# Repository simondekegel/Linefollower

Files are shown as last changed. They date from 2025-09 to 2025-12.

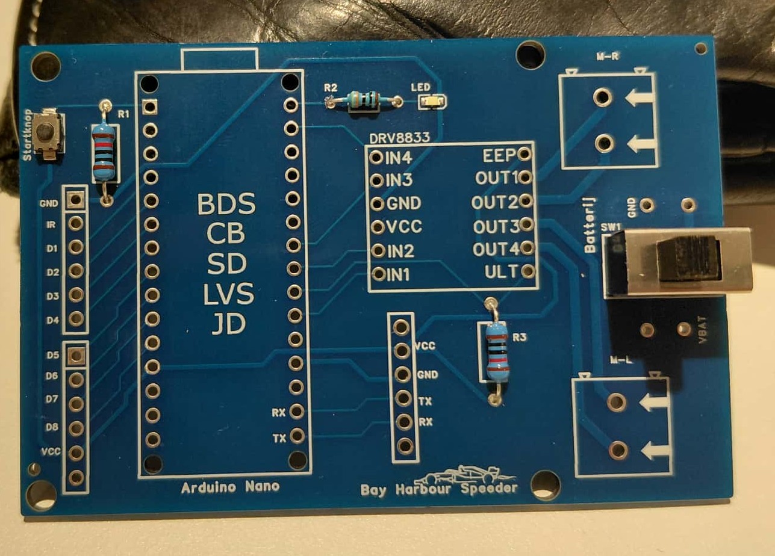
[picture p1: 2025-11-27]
images/519357136-53358113-0e21-4ff5-8163-3b82a2c3a71a.jpeg

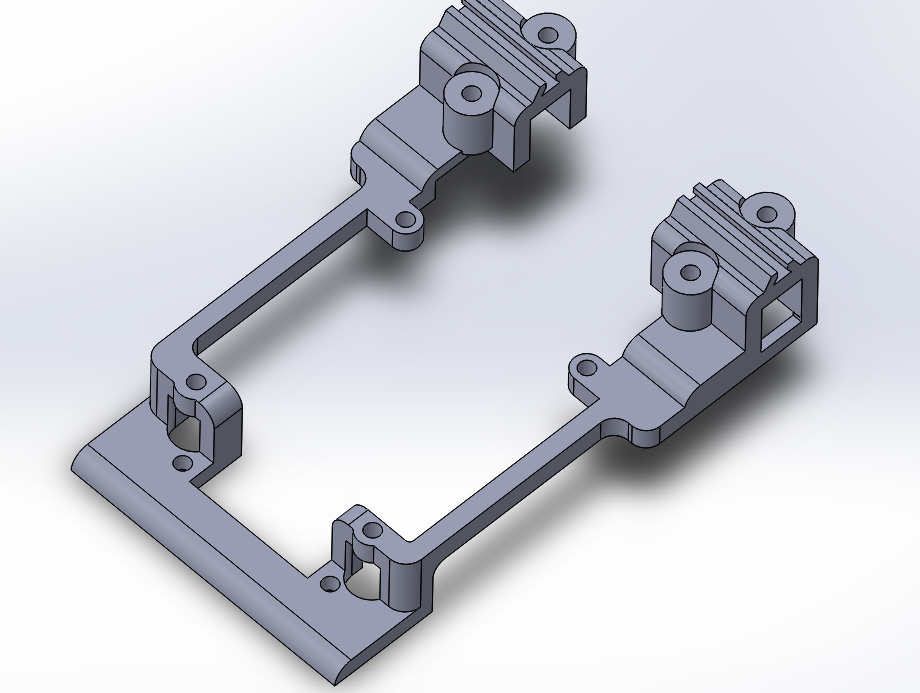
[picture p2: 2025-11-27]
technische tekeningen/mechanisch/517844766-8e0d4717-322a-4456-812b-64dfd0e3311b.png

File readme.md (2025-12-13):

# LineFollower

516304872-0ebdff40-2b66-4d8c-be46-cdccf1087acf

## specifications

microcontroller: Arduino nano (clone)

motors: N20---30:1---500RPM 

h-bridge: DRV8833

sensors: HY-S301

batteries: 2x 18650 lipo

wireless communication: HC-08 

distance sensor - motors: 9.92cm

weight: 214gr

speed: 0.72m/s

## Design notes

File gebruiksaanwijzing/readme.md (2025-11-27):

# Gebruiksaanwijzing

### opladen / vervangen batterijen
Batterijen worden opgeladen met een lader die specifiek ontworpen is voor 18650 (Lithium) batterijen.
Voor de batterijen kunnen worden ingestoken of verwijderd moet er gecontroleerd worden of de hoofdschekelaar van de pcb uitstaat (naar buitenste stand van de schakelaar)

### draadloze communicatie
#### verbinding maken
We gebruiken een Hc-08, deze kan een signaal spanning aan van 3,2-6V op zijn TX & RX pinnen. En 3,2-6V op zijn VCC. 

Een Hc-08 werkt op BLE (Bluetooth low energy), deze is dus compatible voor zowel android als iphone apparaten.

De applicatie die gebruikt werdt om de commandos te sturen is "serial bluetooth terminal", is beschikbaar op de google playstore en zou ook op de iphone app store beschikbaar moeten zijn.

#### commando's
debug : debug

start : run on

stop  : zolang je een niet bekend commande typed zal hij stoppen

set cycle [µs]  : set cycle ...

set power [0..255]  : set power ...

set diff [0..1]  : set diff ...

set kp [0..]  set kp ...

set ki [0..]  set ki ...

set kd [0..]  set kd ...

calibrate black  : calibrate black

calibrate white  : calibrate white

### kalibratie
uitleg kalibratie  

### settings
De robot rijdt stabiel met volgende parameters: 

| KP: 30  | KI: 0.1 | KD: 0.35 | diff:  0.6 | Power: 130 | snelheid: 0.63m/S |

### start/stop button
De start knop is aanwezig op de pcb, deze is geplaatst naast de sensoren (rechts voor). Deze knop zal de zelfde variable sturen als het commando run on. Om de follower te doen stoppen kan je een commande sturen of hem boven een wit blad houden (dit is zodat hij stopt met rijden als hij geen zwarte lijn meer ziet).

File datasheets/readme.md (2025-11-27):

datasheets of the components used in this project

Datasheet van de DRV8833 [drv8833-datasheet.pdf](https://github.com/user-attachments/files/23694670/drv8833-datasheet.pdf)

Datascheet van de Arduino nano [A000005-datasheet.pdf](https://github.com/user-attachments/files/23694715/A000005-datasheet.pdf)

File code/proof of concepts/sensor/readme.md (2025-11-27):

# Sensoren proof of concept
minimale hard- en software die aantoont dat minimaal 6 sensoren onafhankelijk van elkaar kunnen uitgelezen worden (geen calibratie, normalisatie of interpolatie). Hierbij moet een zo groot mogelijk bereik van de AD converter benut worden (indien van toepassing)

Benodigdheden

HY-S301
Arduino Nano R3
Stappenplan

Sluit de sensor aan de arduino volgens het aansluitschema aan.
Verbind de arduino met de pc en upload het programma in de arduino.
test met een wit oppervlak of de waarden veranderen van de sensoren.

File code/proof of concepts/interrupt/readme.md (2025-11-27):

# start/stop interrupt proof of concept
Dit is een simpele minimale code die aantoont hoe da een toggle functie kan geprogrammeerd worden met een knop en led. 
Uitgangen zijn gekozen a.d.h.v. het elektronisch schema.

De knop wordt uitgelezen en zal een bool (run) op initieel op 1 zetten bij het 1ste gebruik.
Bij de 2de druk, als run = 1, zal diezelfde knop run op 0 zetten waardoor de led ook zal doven.

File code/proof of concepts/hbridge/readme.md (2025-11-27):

# H-Bridge proof of concept

Welkom in de readme van het H-brug gedeelte van de linefollower.

De H-brug gebruikt een DRV8833 microchip. Deze heeft op het breakoutbord 4 ingangen, 4 uitgangen, VCC, GND, EEP & ULT.

De ingangen en uitgangen spreeken opzich, zeer belangrijk bij de ingangen is dat de pwm's op de zelfde clock snelheid zitten. PWM 3, 5, 6 & 11 hebben een 8bit clocksnelheid. PWM 9 & 10 hebben een 16bit clocksnelheid. ALs 2 soorten clocksnelheden worden gebruikt zullen de motoren een verschillende snelheid hebben.

De EEP pin wordt aan de VCC (5V) van de arduino gekoppeld, dit moet zeker verbonden worden anders zal de H-brug niet werken. Als de EEP geen voeding krijgt zal de H-brug in sleep modus staan waardoor de OUT's niet zullen schakelen.

De Ult pin wordt met een pull-up weerstand geschakeld, deze dient als fout detectie. Als de H-brug normaal werkt zal deze een hoog signaal hebben waardoor de arduino een laag signaal leest. Als er een interne fout in de H-brug is zal de uitgang laag zijn waardoor de arduino een hoog signaal zal lezen. Dit zullen we a.d.h.v. een HC-05 door sturen naar een gsm.

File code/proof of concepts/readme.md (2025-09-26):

# Proof of Concepts

Een proof of concept is een combinatie van minimale hard- en software om eenvoudig aan te tonen dat iets werkt.  
Proof of concepts kunnen enerzijds als eerste poging dienen om een bepaald onderdeel van het project werkend te krijgen. Anderzijds kunnen ze tijdens het debuggen van het finale project dienen als test om eventuele hardware problemen te elimineren bij onduidelijke problemen.
<br />  
<br />
Een proof of concept bestaat uit
* een elektronisch schema (indien van toepassing)
* minimale code om de voorop gestelde zaken te demonstreren
* minimale uitleg / aandachtspunten
<br />
De elektronische schakelingen van de proof of concepts komen bij voorkeur overeen met deze van de uiteindelijke linefollower, zodat de code zonder aanpassingen op het finale project kan draaien.

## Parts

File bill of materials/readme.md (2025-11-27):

## bill of materials
<br />

|volgnummer|naam|omschrijving|nieuw/recup|kostprijs/stuk|aantal|subtotaal|
|---|----|---|---|---|---|---|
| 1| HC-08 Bluetooth module met adapter - clone| bluetooth module | nieuw | €8.5 |  1 |  €8.5 |
| 2| Arduino Nano R3 - kloon - met headers| Arduino Nano | nieuw |  €8.60 |  1 |  €8.60 |
| 3| Female header stackable 6 pin (5x nodig) |10x Female headers 6 pin | nieuw |  €2.85 | 0.5 | €1.425 |
| 4| DRV8833|dubbele H-brug | nieuw | €3 | 1 |€3 |
| 5| HY-S301 | 8x IR Lijn Tracking Module | nieuw | €3.50 | 1 | €3.50 |
| 6| Aslong JGA12-N20-30 DC-Transmissiemotor 6V - 500RPM| motor 30:1 | nieuw |  €4.50 | 2 |  €9.00 |
| 7| 15 Pins header Female | fermale headers 15 pinss | nieuw |  €0.31 | 2 | €0.62 |
| 8| 18650 | batterij | nieuw | €1.45 | 2 | €2.90 |
| 9| 2x 18650 Batterijhouder met klemkontacten en losse draden | Batterijhouder |  nieuw | €1.59 | 1 |  €1.59 |
| 11| | klemschroefblok 2 pins | recup | €0.55 |  2 |  €1.10 |
| 12| JLCPCB| zelf ontworpen pcb | nieuw | €4.245 |  1 | €4.245 |
| 13|  wielen  | aliexpress wielen | nieuw | €0.98 |  2 | €1.96 |
| | | | | | | |
| Tootaal| |  (zonder verzend kosten!!!!!) | | | | €46,44 |

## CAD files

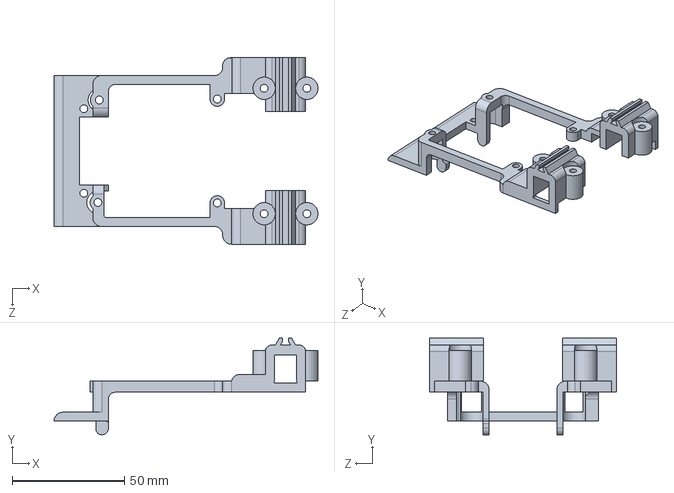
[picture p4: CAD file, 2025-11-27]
technische tekeningen/mechanisch/Frame V9.SLDPRT
117.5 x 43.0 x 83.0 mm

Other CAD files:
technische tekeningen/mechanisch/Frame V9.STL

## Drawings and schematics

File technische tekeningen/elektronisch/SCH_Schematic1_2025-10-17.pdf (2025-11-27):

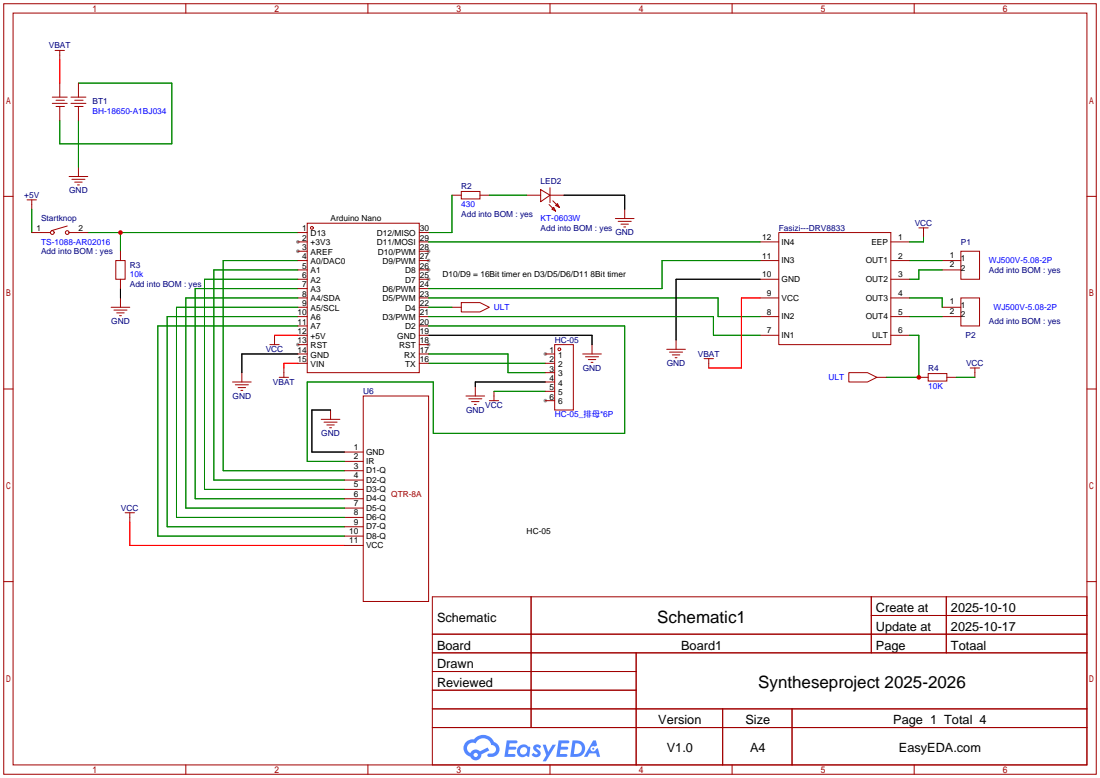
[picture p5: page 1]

Startknop
Add into BOM : yes

Schematic | Schematic1 | Create at | 2025-10-10

Update at | 2025-10-17

Board | Board1 | Page | Totaal
Drawn | | Syntheseproject 2025-2026
Reviewed

Version | Size | Page 1 Total 4
V1.0 | A4 | EasyEDA.com

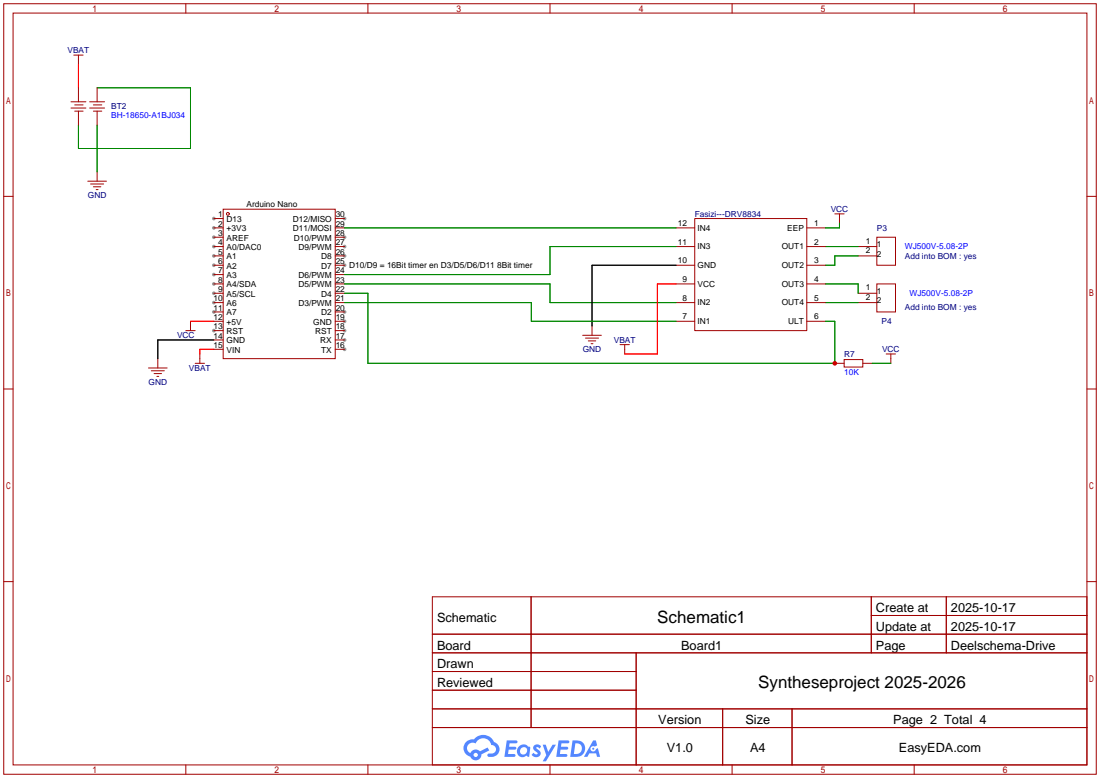
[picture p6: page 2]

Schematic | Schematic1 | Create at | 2025-10-17

Update at | 2025-10-17

Board | Board1 | Page | Deelschema-Drive
Drawn | | Syntheseproject 2025-2026
Reviewed

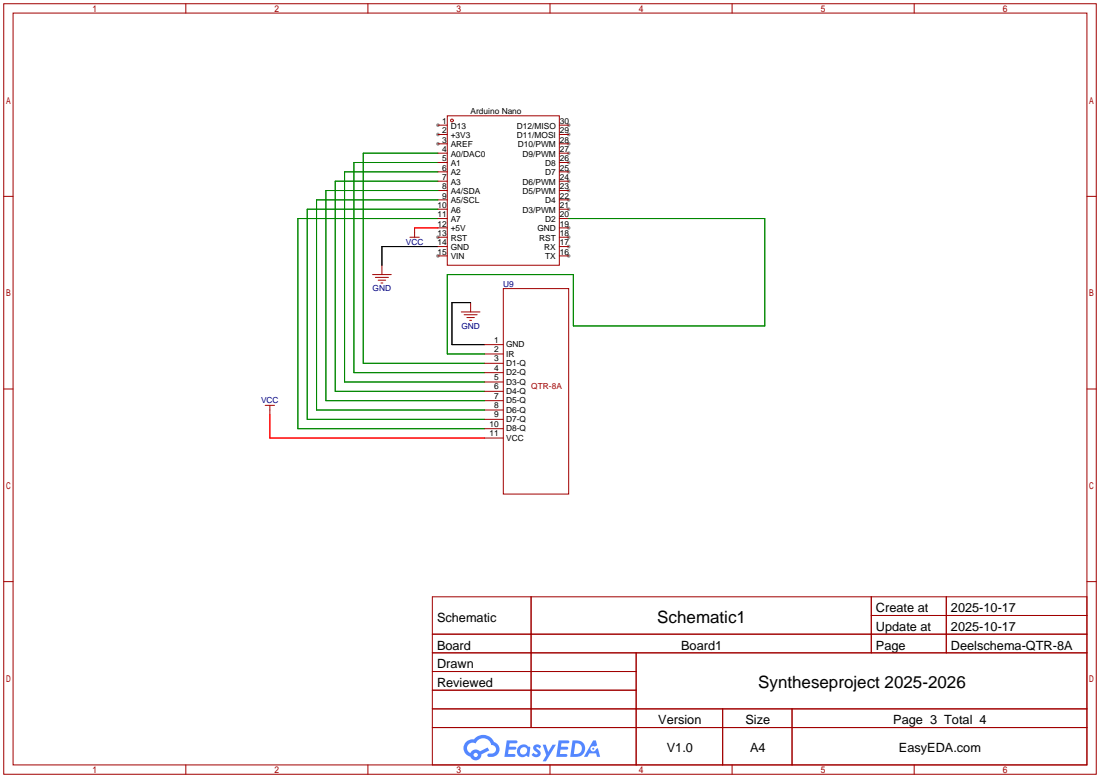
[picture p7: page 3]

Schematic | Schematic1 | Create at | 2025-10-17

Update at | 2025-10-17

Board | Board1 | Page | Deelschema-QTR-8A
Drawn | | Syntheseproject 2025-2026
Reviewed

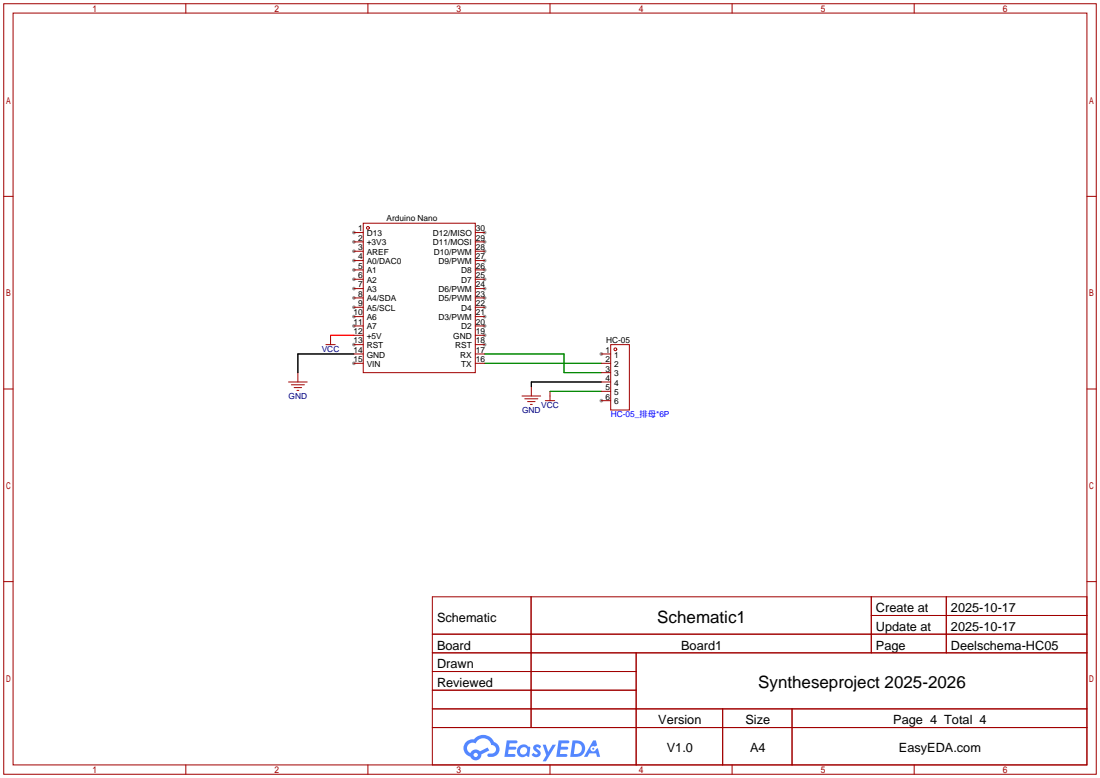
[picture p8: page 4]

Schematic | Schematic1 | Create at | 2025-10-17

Update at | 2025-10-17

Board | Board1 | Page | Deelschema-HC05
Drawn | | Syntheseproject 2025-2026
Reviewed

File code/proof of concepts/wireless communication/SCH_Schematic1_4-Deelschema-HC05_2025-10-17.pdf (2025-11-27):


Schematic | Schematic1 | Create at | 2025-10-17

Update at | 2025-10-17

Board | Board1 | Page | Deelschema-HC05
Drawn | | Syntheseproject 2025-2026
Reviewed

Version | Size | Page 4 Total 4
V1.0 | A4 | EasyEDA.com

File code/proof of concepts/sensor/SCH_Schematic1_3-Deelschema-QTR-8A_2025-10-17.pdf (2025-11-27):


Schematic | Schematic1 | Create at | 2025-10-17

Update at | 2025-10-17

Board | Board1 | Page | Deelschema-QTR-8A
Drawn | | Syntheseproject 2025-2026
Reviewed

Version | Size | Page 3 Total 4
V1.0 | A4 | EasyEDA.com

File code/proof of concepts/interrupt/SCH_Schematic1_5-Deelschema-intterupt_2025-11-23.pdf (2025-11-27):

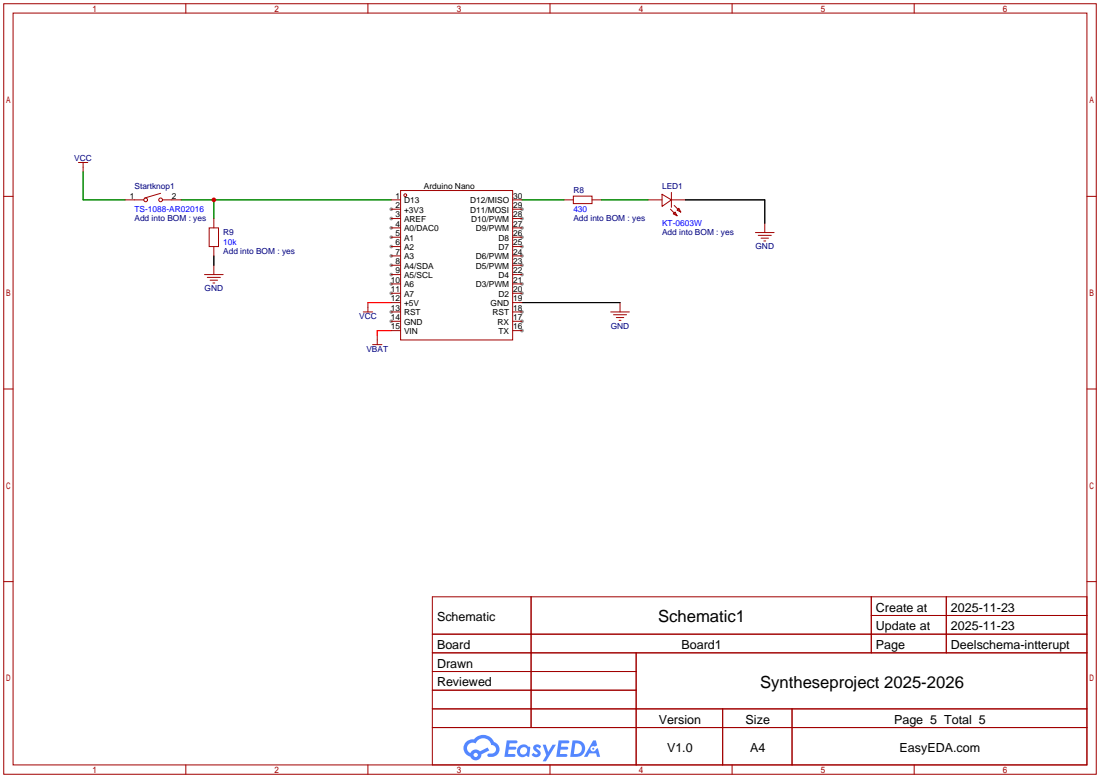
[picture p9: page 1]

Add into BOM : yes

Schematic | Schematic1 | Create at | 2025-11-23

Update at | 2025-11-23

Board | Board1 | Page | Deelschema-intterupt
Drawn | | Syntheseproject 2025-2026
Reviewed

Version | Size | Page 5 Total 5
V1.0 | A4 | EasyEDA.com

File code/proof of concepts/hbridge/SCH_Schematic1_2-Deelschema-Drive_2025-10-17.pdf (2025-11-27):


Schematic | Schematic1 | Create at | 2025-10-17

Update at | 2025-10-17

Board | Board1 | Page | Deelschema-Drive
Drawn | | Syntheseproject 2025-2026
Reviewed

Version | Size | Page 2 Total 4
V1.0 | A4 | EasyEDA.com

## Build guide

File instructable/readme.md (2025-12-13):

# Instructable

Een instructable is een stappenplan - zonder verdere uitleg - hoe je vertrekkend van de bill of materials en gebruik makend van de technische tekeningen de robot kan nabouwen. Ook de nodige stappen om de microcontroller te compileren en te uploaden staan beschreven.  

### stap 0
Bestel de componenten uit de BOM, zoveel mogelijk van dezelfde leverancier (tinytronics).

De pcb, onder technische tekeningen -> elektronisch vindt je de elektronische schemas als de pcb file die je kan importeren in easyeada.

De pcb is ontworpen om de weerstanden, drukknop, schakelaar en led er op telaten zetten tijdens productie en is dus mee gerekend in de pcb kosten.
(dit moet je tijdens het bestellen aanduiden want dit wordt niet automatisch gedaan)

### stap 1
test de componenten uit a.d.h.v. de schemas en codes onder de tab code -> proof of concepts. 
deze zullen een goede werking demonstreren van de componenten.

DRV8833 wordt best eerst getest met led's.
Aangeraden om de sensor op een vaste hoogt te monteren om een duidelijk verschil te zien tussen zwart en wit.

### stap 2
Soldeer de female headerds en terminals op de pcb als de draden op de sensor, aangeraden om 0.8mm² stijvedraden te gebruiken (recup van sgg kabel).

### stap 3
Print het frame dat te vinden is onder technische tekeningen -> mechanisch. 
Hier zal je een stl bestand vinden als een solidworks tekening voor als je zelf aanpassingen wilt uitvoeren.
(spoiler stl is ook beschikbaar)

### stap 4
monteer alle componeten op het frame met M3 bouten en moeren. je moet er maar 5 van elk gebruiken (2 voor de sensor, 2 voor de batterijhouder en 1 voor de pcb).

### stap 5
Als de motoren en batterijhouder op het frame zijn bevestigd kan je de draden hiervan solderen.

LET GOED OP!!!!
Batterijhouder: de rode draden van de batterijhouder zullen wij zien als + en zwart als -. We solderen de rode draden op de pcb links van de schakelaar (aan de kant waar VBAT staat) en de zwarte draden rechts van de schakelaar (aan de kant waar GND staat). 
De batterijen zijn via de pcb in serie geschakeld dus we mogen ze extern NIET KRUISEN, ik heb de buitenste batterij aan de buitenste pads gesoldeerd en de batterij aan de binnen kant aan de binnenste pads.

Motoren: de motoren kunnen simpel gesoldeerd worden als ze geklemmed zitten in het frame. hoe dat deze aangesloten worden is de bovenste draden aan de buitenste terminal slots en de onderste aan de binneste slots van hun respectievelijke terminals (links-links & rechts-rechts).

### stap 6 
Upload de basis code dat te vinden is in code->basis. download alle 4 de bestanden en zet deze in dezelfde map. anders zal het programma niet werken.
dit programma bevat een basis werking van het EEPROM geheugen als normalistatie en interpolatie van de sensor en een P regelaar. 

commandes zijn terug tevinden in de gebruikersaanwijzing.

### stap 7
print de parcours. steek de batterijen in de houder (ROOD +, ZWART -) en zet de schakelaar naar binnen toe. 
als alles goed is verlopen zullen nu signalisatie leds van de arduino nano, hc-08 en motordrive branden.

### stap 8
zet de follower op een wit stuk van het parcour en calibreer wit, doe dit ook voor zwart.

Zet intitieel  power= 80, kp= 10 en diff op 0,4.
Nu ben je klaar om te rijden. 
Stuur het commande "run on" and watch the magic happen.

Je zal de instellingen langzaam moeten tweaken want de waarde zullen voor iedereen verschillen.

### stap 9
upload de final code, deze heeft ook een I & D regelaar.
De follower heeft nu de mogelijkheid om de lijn vlotter tevolgen.

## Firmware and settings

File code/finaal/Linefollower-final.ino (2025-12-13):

/*
 ----------INSTRUCTIES HOE JE DEZE CODE GEBRUIKT EN WAARDES AANPAST------------
 -----------------------------------CB-----------------------------------------
 voor de waardes intestellen (diff, power, cycle,...) stuur je in de serial monitor => "set (naam) (value)"
 voor het instellen van de cyletime stuur in de serial monitor "set cyle 1000000", cycle time voor goede werking <500
 *
 voor calibratie sensor wit stuur in serial monitor "calibrate white" ----aangeraden om voor elk gebruik opnieuw tedoen, waardes kunnen veelverschillen afhankelijk van omgeving
 voor calibratie sensor zwart stuur in serial monitor "calibrate black" ----aangeraden om voor elk gebruik opnieuw tedoen, waardes kunnen veelverschillen afhankelijk van omgeving
 *
 om de opgeslagen waarden van het eeprom geheugen te controleren stuur je in de serial monitor "debug"
 diff <0.5 anders gaat er 1 van de motoren niet achteruit!!! (fysiek motor rechts, in de programmatie is dit motor links, ben te lui om dit aantepassen)
 *
 
*/
#include "SerialCommand.h"
#include "EEPROMAnything.h"
#define SerialPort Serial
#define Baudrate 9600
bool run;  // variabele om de line follower aantezetten, zowel fysiek als via de serialmonitor
SerialCommand sCmd(SerialPort);
bool debug = false;
const int sensor[] = { A7, A6, A5, A4, A3, A2, A1, A0 };  //sensoren van links naar rechts
unsigned long previous, calculationTime;
const int led = 12;  // fysieke signalisatie om te weten of run aanstaat
long normalised[8];  //array voor de nieuwe genomaliseerde waardes
const int knop = 13;
float position;  //postie van de bay harbor speeder
int status = 0;
int index = 0;
float debugPosition;
float iTerm, lastErr;
// Motorpins
const int M1_IN1 = 3;
const int M1_IN2 = 5;
const int M2_IN3 = 11;
const int M2_IN4 = 6;
//
//
//EEPROM start
struct param_t  //dit is voor het EEPROM geheugen, deze waardes worden onthouden bij een reset
{
  unsigned long cycletime;
  int black[8];  //waarde sensor zwart
  int white[8];  //waarde sensor wit
  float Kp;
  float Ki;
  float Kd;
  float diff;
  int power;
} params;
//EEPROM stop
//
//
void setup() {
  ADCSRA &= ~((1<<ADPS2) | (1<<ADPS1) | (1<<ADPS0)); // testen, geeft extra ruis
  ADCSRA |= (1<<ADPS2); // testen, geeft extra ruis // geeft stabiele sensor waarde maar een calc time tijdens run van 792µs
  //ADCSRA = (ADCSRA & 0b11111000) | 0b010; //geeft calc tijd van 712µs maar iets minder stabiele sensor waarden 
  SerialPort.begin(Baudrate);
  sCmd.addCommand("set", onSet);
  sCmd.addCommand("debug", onDebug);
  sCmd.setDefaultHandler(onUnknownCommand);
  sCmd.addCommand("calibrate", onCalibrate);
  EEPROM_readAnything(0, params);
  SerialPort.println("ready");
  sCmd.addCommand("run", onRun);
  pinMode(led, OUTPUT);
  pinMode(knop, INPUT);
  status = LOW;
  pinMode(M1_IN1, OUTPUT);
  pinMode(M1_IN2, OUTPUT);
  pinMode(M2_IN3, OUTPUT);
  pinMode(M2_IN4, OUTPUT);
}
//
//
//
void loop() {
  Aanzetten();
  sCmd.readSerial();
  unsigned long current = micros();            // non blokking wait
  if (current - previous >= params.cycletime)  //cycletime in de params (EEPROM) omgeving
  {
    previous = current;
    //normalisatie start
    for (int i = 0; i < 8; i++) {
      long value = analogRead(sensor[i]);
      normalised[i] = map(value, params.black[i], params.white[i], 0, 1024);  //herschaling van de sensor waarden
    }
    //normalisatie einde
    //herbekijk de video interpolatie
    /*volgende code zorgt voor de interpolatie van de sensor waarde. met een bereik van 30 t.e.m. -30 */                                                                                                                                                                                                                                                                                                          if (status == 0){run = 0;}   
    //
    for (int i = 1; i < 6; i++)
      if (normalised[i] < normalised[index]) index = i;
    if (normalised[index] > 500) run = false;  //als de line-follower van de zwarte lijn is zal hij stoppen
    if (index == 0) position = -20;
    else if (index == 5) position = 20;
    else {
      int sNul = normalised[index];
      int sMinEen = normalised[index - 1];
      int sPlusEen = normalised[index + 1];
      float b = sPlusEen - sMinEen;
      b = b / 2;
      float a = sPlusEen - b - sNul;
      position = -b / (2 * a);
      position += index;
      position -= 3.5;
      position *= 15;
    }
    //
    //
    //PID
    if (run == 1)  //Voor de Iterm, zodat deze pas zal werken als de auto actief is, DUBBEL CHECKEN
    {
      debugPosition = position;
      float error = -position;
      float output = error * params.Kp;  // output berekening met Kp
      //
      //I regelaar start
      //iterm mag enkel worden uitgevoerd tijdens het rijden, anders zal deze zeer snel naar zen maximum lopen
      //
      iTerm += params.Ki * error;  // output berekening met Ki
      iTerm = constrain(iTerm, -510, 510);
      output += iTerm;  // zorgt ervoor dat de output geen sprongen maakt als ki opeens van waarde verandert
      // i regelaar einde
      //
      //d-regelaar start
      output += params.Kd * (error - lastErr);
      lastErr = error;
      //einde d-rgelaar
      //
      output = constrain(output, -510, 510);  //-510 & 510 zijn de uiterste pwm waarde met de motoren
      int powerLeft = 0;
      int powerRight = 0;

        if (output >= 0) {
          powerLeft = constrain(params.power + params.diff * output, -255, 255);  //limiteerd de uiterste pwm waarde van de motor
          powerRight = constrain(powerLeft - output, -255, 255);                  //limiteerd de uiterste pwm waarde van de motor
          powerLeft = powerRight + output;
        } else {
          powerRight = constrain(params.power - params.diff * output, -255, 255);  //limiteerd de uiterste pwm waarde van de motor
          powerLeft = constrain(powerRight + output, -255, 255);                   //limiteerd de uiterste pwm waarde van de motor
          powerRight = powerLeft - output;
        }
      analogWrite(M1_IN1, powerLeft > 0 ? powerLeft : 0);
      analogWrite(M1_IN2, powerLeft < 0 ? -powerLeft : 0);
      analogWrite(M2_IN3, powerRight > 0 ? powerRight : 0);
      analogWrite(M2_IN4, powerRight < 0 ? -powerRight : 0);
    }
    if (run == 0) { 
      digitalWrite(led, LOW);
      analogWrite(M1_IN1, LOW);
      analogWrite(M1_IN2, LOW);
      analogWrite(M2_IN3, LOW);
      analogWrite(M2_IN4, LOW);
     }
    unsigned long difference = micros() - current;                   //-----geen idee wat dit doet
    if (difference > calculationTime) calculationTime = difference;  //-----geen idee wat dit doet
  }
}
//
//
//
void onUnknownCommand(char* command)  //dit deel wordt uitgevoerd als onbekende commandos worden geschreven in de serialmonitor
{
  SerialPort.print("unknown command: \"");
  SerialPort.print(command);
  SerialPort.println("\"");
  run = false;
  
}
//
//
//
void onSet()  //dit deel wordt uitgevoerd als set wordt geschreven in de serialmonitor
{
  char* param = sCmd.next();
  char* value = sCmd.next();
  // als KI niet werkt -> if (strcmp(param, "cycle") == 0) params.cycletime = atol(value) ; //debug = false;
  //
  //KI om te testen, berekend ki a.d.h.v. eenheid per seconde (moet getest worden)
  if (strcmp(param, "cycle") == 0) {
    long newCycleTime = atol(value);
    float ratio = ((float)newCycleTime) / ((float)params.cycletime);

    params.Ki *= ratio;
    params.Kd /= ratio;

    params.cycletime = newCycleTime;
  } 
  
  else if (strcmp(param, "ki") == 0) {
    float cycleTimeInSec = ((float)params.cycletime) / 1000000;
    params.Ki = atof(value) * cycleTimeInSec;
  }
  //einde ki berekenen
  //kd
   else if (strcmp(param, "kd") == 0)
  {
    float cycleTimeInSec = ((float) params.cycletime) / 1000000;
    params.Kd = atof(value) / cycleTimeInSec;
  }
  
  //
  else if (strcmp(param, "power") == 0)
    params.power = atol(value);
  else if (strcmp(param, "kp") == 0) params.Kp = atof(value);      //Kp is een float
  else if (strcmp(param, "diff") == 0) params.diff = atof(value);  //diff is een float
  EEPROM_writeAnything(0, params);
}
//
//
//
void onDebug()  // debug, hier komen de belangrijke waarden om te debuggen
{
  SerialPort.print("cycle time: ");
  SerialPort.println(params.cycletime);

  SerialPort.print("calculation time: ");
  SerialPort.println(calculationTime);
  calculationTime = 0;

  //
  SerialPort.print("black: ");
  for (int i = 0; i < 7; i++) {
    SerialPort.print(params.black[i]);
    SerialPort.print(" ");
  }
  SerialPort.println(" ");
  //
  SerialPort.print("white: ");
  for (int i = 0; i < 7; i++) {
    SerialPort.print(params.white[i]);
    SerialPort.print(" ");
  }

  SerialPort.println(" ");
  //
  Serial.print("position: ");
  Serial.println(position);
  //
  Serial.print("run: ");
  Serial.println(run);

  SerialPort.print("Kp: ");
  SerialPort.print(params.Kp);
  SerialPort.println(" ");

  SerialPort.print("power: ");
  SerialPort.print(params.power);
  SerialPort.println(" ");

  SerialPort.print("diff: ");
  SerialPort.print(params.diff);
  SerialPort.println(" ");
  //
  //Geeft Ki terug met eenheid per sconde (moet getest worden)
  float cycleTimeInSec = ((float)params.cycletime) / 1000000;
  float ki = params.Ki / cycleTimeInSec;
  SerialPort.print("Ki: ");
  SerialPort.println(ki);
  //kd
   float kd = params.Kd * cycleTimeInSec;
  SerialPort.print("Kd: ");
  SerialPort.println(kd);
  
  //
}
//
//
//
void onCalibrate()  //calibratie voor de sensor
{
  char* param = sCmd.next();
  digitalWrite(led, HIGH);

  if (strcmp(param, "black") == 0)  //calibratie als "black" wordt geschreven
  {
    SerialPort.print("start calibrating black... ");
    for (int i = 0; i < 8; i++) params.black[i] = analogRead(sensor[i]);
    SerialPort.println("done");
  } else if (strcmp(param, "white") == 0)  //calibratie als "white" wordt geschreven
  {
    SerialPort.print("start calibrating white... ");
    for (int i = 0; i < 8; i++) params.white[i] = analogRead(sensor[i]);
    SerialPort.println("done");
  }

  EEPROM_writeAnything(0, params);
}
//
//
//
void Aanzetten() {
  if (run == false) {
    if (digitalRead(knop) == 1) {
      run = true;
      digitalWrite(led, HIGH);
    }
  }
}
//
//
//
void onRun() {
  char* parameter = sCmd.next();
  char* value = sCmd.next();
  if (strcmp(parameter, "on") == 0) {
    iTerm = 0;
    run = true;
    digitalWrite(led, HIGH);
  } else run = false;
}

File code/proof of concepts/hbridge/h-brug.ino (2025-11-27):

const int IN1 = 5;   // Motor A pin 1
const int IN2 = 6;   // Motor A pin 2
const int IN3 = 9;   // Motor B pin 1
const int IN4 = 10;  // Motor B pin 2

void setup() {
  pinMode(IN1, OUTPUT);
  pinMode(IN2, OUTPUT);
  pinMode(IN3, OUTPUT);
  pinMode(IN4, OUTPUT);
  Serial.begin(9600);
  Serial.println("Twee motoren snelheidsverloop test start");
}

void loop() {
  // snelheid van -255 (achteruit) naar 255 (vooruit)
  for (int snelheid = -255; snelheid <= 255; snelheid++) {
    stelMotorSnelheidIn(IN1, IN2, snelheid);  // Motor A
    stelMotorSnelheidIn(IN3, IN4, snelheid);  // Motor B
    Serial.println(snelheid);
    delay(10); // bepaalt hoe snel de verandering verloopt
  }

  // eventueel even stoppen
  stelMotorSnelheidIn(IN1, IN2, 0);
  stelMotorSnelheidIn(IN3, IN4, 0);
  delay(1000);
}

// ---------- Functie om motorrichting en PWM in te stellen ----------
void stelMotorSnelheidIn(int pin1, int pin2, int snelheid) {
  if (snelheid > 0) {
    analogWrite(pin1, snelheid);
    analogWrite(pin2, 0);
  } else if (snelheid < 0) {
    analogWrite(pin1, 0);
    analogWrite(pin2, -snelheid); // negatief omzetten naar positief
  } else {
    // motor uit
    analogWrite(pin1, 0);
    analogWrite(pin2, 0);
  }
}
